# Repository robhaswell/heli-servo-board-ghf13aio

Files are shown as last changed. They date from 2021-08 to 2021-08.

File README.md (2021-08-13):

# Helicopter servo bus board
This project is a PCB designed to facilitate wiring a helicopter servo bus to a drone flight controller.

Mounting pattern: 16x16mm

The flight controller in mind when designing this PCB was a [GHF13AIO](https://www.aliexpress.com/af/ghf13aio.html).
This bus supports 3 servo outputs and so must be used for helicopters with a motor-driven tail connected to an ESC.

The connector footprints are for 1.25mm pitch connectors, such as Molex PicoBlade or JST 1.25.

**Please read the [assembly instructions](#assembly-instructions) before ordering or use**

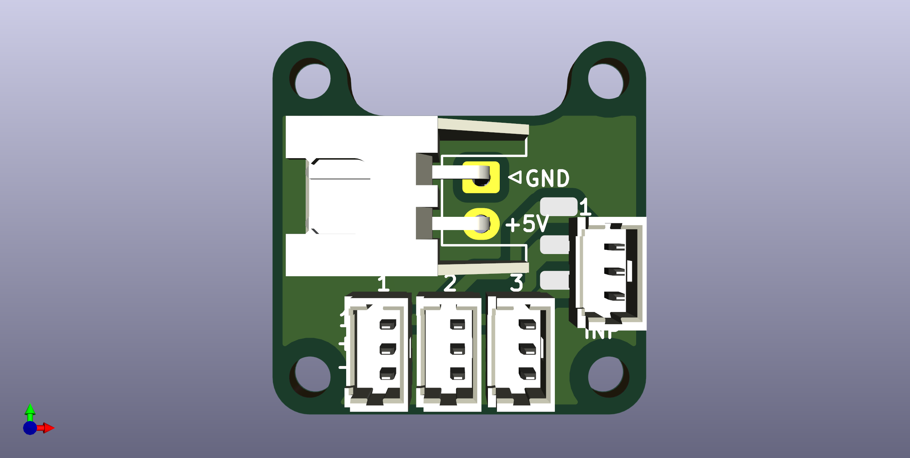
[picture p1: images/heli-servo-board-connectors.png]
PCB render with connectors

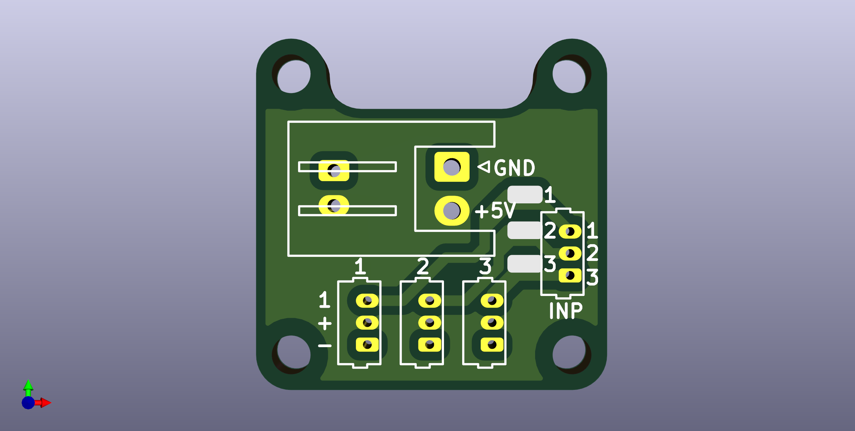
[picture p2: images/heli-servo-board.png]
PCB render without connectors


## Instructions for ordering

First: Read the [assembly instructions](#assembly-instructions) and determine that this board is suitable for your setup.

You can order this PCB with a prototyping service.
Below are instructions for using [JLCPCB](https://jlcpcb.com):

1. Visit https://jlcpcb.com/.
2. Click "Order now' from the menu - do not use the quoting box.
3. Upload the file [gerber.zip](gerber.zip).
4. You may use the default options, but I suggest selecting a thickness of 0.8mm or 1.0mm. I also prefer the black PCBs.
5. Add to basket and check out. Take care to review the shipping options. FedEx is good if you would like this sooner, but there is usually a very cheap option depending on your location.

## Assembly instructions

To assemble you will need:

1. PicoBlade or JST 1.25 connectors to match your servo plugs.
2. JST-XH 2-way horizontal connector `S2B-XH-A(LF)(SN)`  
or  
JST-XH vertical or other 2.54mm connector.  
or  
JST-PH or other 2.00mm connector.

**Pay very close attention to plug wiring, pins and polarities!!!**

There are no standard servo plug pinouts.
Test everything with a multimeter before soldering, and again before powering on.

1. Make sure that your intended servos have the control wire as pin 1 or 3.
2. Solder your servo input connector, or use the solder pads directly. These are the control lines from your PWM servo outputs on your FC. If using solder pads you can solder directly to the wire pads, connector pads, or both. Use silicone glue to secure the wire.
3. Solder your servo connectors so that the control wire is the topmost pin, the row labelled "1".
4. Check the position of your servo positive and negative wires. They should line up with "+" and "-". If they do not (e.g. Blade servos) then you will need to re-pin your power connector or wire it in reverse.
5. Check the pins of your power connector and verify correct pins with a multimeter, then solder.
6. Test all connections a final time.

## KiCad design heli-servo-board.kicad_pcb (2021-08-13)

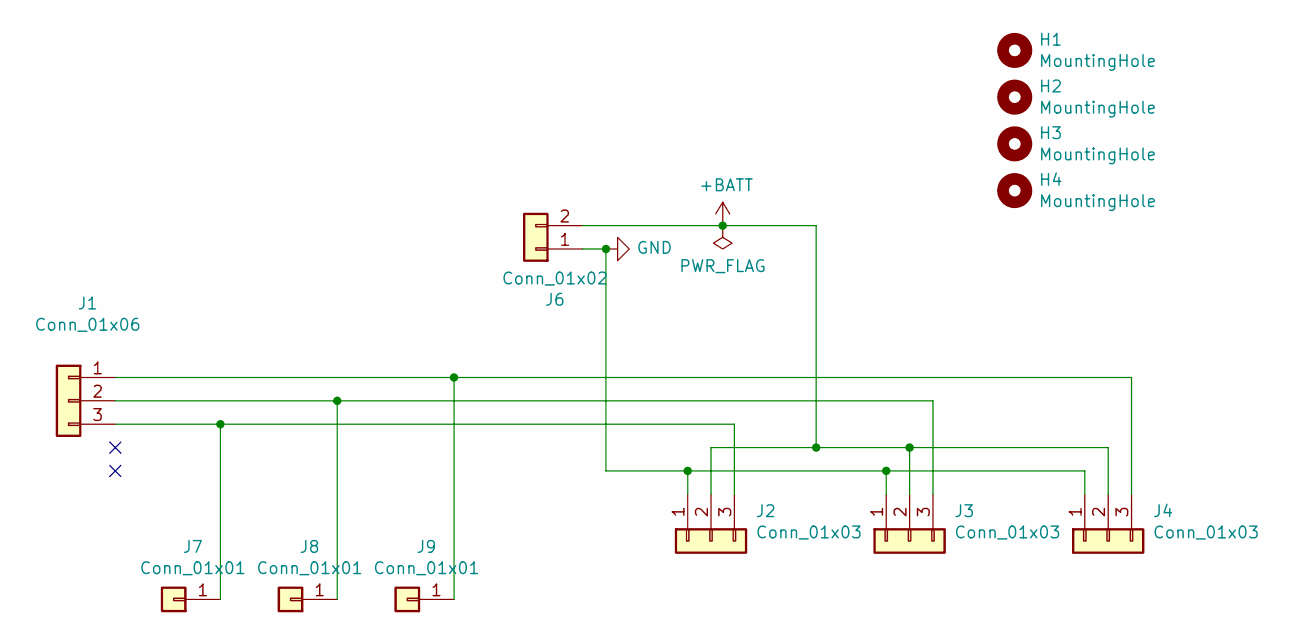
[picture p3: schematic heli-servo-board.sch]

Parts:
H1, H2, H3, H4: MountingHole; MountingHole_2.2mm_M2
J1: Conn_01x06; Molex_PicoBlade_53047-0310_1x03_P1.25mm_Vertical
J2, J3, J4: Conn_01x03; Molex_PicoBlade_53047-0310_1x03_P1.25mm_Vertical
J6: Conn_01x02; JST_XH_S2B-XH-A_1x02_P2.50mm_Horizontal
J7, J8, J9: Conn_01x01; SolderWirePad_1x01_SMD_1x2mm

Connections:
+BATT: J2.2, J3.2, J4.2, J6.2
GND: J2.1, J3.1, J4.1, J6.1
unnamed: J1.1, J4.3, J9.1
unnamed: J1.2, J3.3, J8.1
unnamed: J1.3, J2.3, J7.1

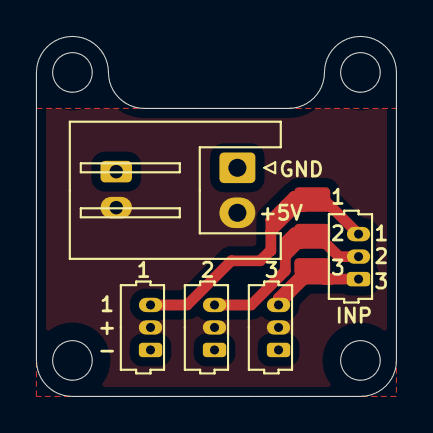
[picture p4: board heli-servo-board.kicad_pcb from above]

Board: 2 copper layers, 20.0 x 20.0 mm, 12 parts (0 on the bottom side), 5 nets.

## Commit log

2021-08-12 Initialise repo with finished servo board.
    [heli-servo-board-B_Cu.gbr, heli-servo-board-B_Mask.gbr, heli-servo-board-B_Paste.gbr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]
2021-08-12 Add 2.0mm power connectors.
    [heli-servo-board-B_Cu.gbr, heli-servo-board-B_Mask.gbr, heli-servo-board-B_Paste.gbr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]
2021-08-12 The GHF13AIO is actually 16x16mm, redesigned with this mistake corrected
    [heli-servo-board-B_Cu.gbr, heli-servo-board-B_Mask.gbr, heli-servo-board-B_Paste.gbr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]
2021-08-12 Slightly adjust XH horizontal position.
    [heli-servo-board-B_Cu.gbr, heli-servo-board-B_Mask.gbr, heli-servo-board-B_Paste.gbr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]
2021-08-12 Beter PCB traces.
    [heli-servo-board.kicad_pcb]
2021-08-12 Overdo the traces.
    [heli-servo-board-B_Cu.gbr, heli-servo-board-B_Mask.gbr, heli-servo-board-B_Paste.gbr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]
2021-08-13 Fix Y dimension.
    [heli-servo-board-B_Cu.gbr, heli-servo-board-B_Mask.gbr, heli-servo-board-B_Paste.gbr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]
2021-08-13 Add K110 tail mount.
    [heli-servo-board.kicad_pcb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]
